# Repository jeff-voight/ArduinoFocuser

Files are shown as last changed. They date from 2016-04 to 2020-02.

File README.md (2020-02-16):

# ArduinoFocuser
My homemade Arduino Focuser

### Parts List
|ID				|#	|Name					|Type								|Module										|Description|
| ---			| ---	| ---					| ---								| ---										| ---										|
|A1				|1	|Arduino_UNO_R3			|MCU_Module:Arduino_UNO_R3			|Module:Arduino_UNO_R3						|Arduino UNO Microcontroller Module, release 3|
|C1, C2, C3		|3	|.01uF					|Device:C							|Capacitor_THT:C_Disc_D3.0mm_W2.0mm_P2.50mm	|Unpolarized capacitor|
|DRV1			|1	|Pololu_Breakout_DRV8825|Driver_Motor:Pololu_Breakout_DRV8825|Module:Pololu_Breakout-16_15.2x20.3mm		|Pololu Breakout Board, Stepper Driver DRV8825|
|Motor1			|1	|Stepper_Motor_bipolar	|Motor:Stepper_Motor_bipolar		|TerminalBlock:TerminalBlock_bornier-4_P5.08mm|4-wire bipolar stepper motor|
|R1, R2, R3, R4	|4	|10k					|Device:R							|Resistor_THT:R_Axial_DIN0204_L3.6mm_D1.6mm_P5.08mm_Horizontal|Resistor|
|SW1			|1	|Rotary_Encoder_Switch	|Device:Rotary_Encoder_Switch		|Rotary_Encoder:RotaryEncoder_Alps_EC11E-Switch_Vertical_H20mm|Rotary encoder, dual channel, incremental quadrate outputs, with switch|
|U1				|1	|DHT11					|Sensor:DHT11						|Sensor:Aosong_DHT11_5.5x12.0_P2.54mm		|Temperature and humidity module|
|U2				|1	|SN74HC14N				|dk_Logic-Gates-and-Inverters:SN74HC14N|digikey-footprints:DIP-14_W3mm			|IC INVERTER SCHMITT 6CH 14DIP|

* One (1) case of your choosing (plans for printing a sloppy case are included in the project)
* One (1) Motor mount (PDF somehwere around here for a 18ga steel bracket you can drill and bend yourself)
* One (1) coupler (I went with a 4mm x 6mm flexible coupler and drilled it to fit my shafts)
* One (1) 12VDC 2A power supply (wall-wart. You're just plugging it in to the Arduino UNOr3)
* Solder, wires, 4 pin connectors for as many scopes as you have.
* One long USB-A to USB-2 cable (or whatever the distance is from your laptop USB hub to where the focuser box will sit plus tripping slack)

# Things you'll want to change in the code:
My telescope focuser knob turns 5.75 times to go from end to end and moves some 13cm (or was it 23?). EncoderPositioner.h and StepperMotor.h are important.

For now, there may very-well be hardcoded values in the cpp files. I highly recommend you walk through them before applying bizarre amounts of
torque to your telescope focuser rod.

# To do:
* I want to add a limit switch to the motor end of the focus tube to detect the zero point. I haven't figured out how I want to impliment this. Maybe have the
focuser rack all the way closed on startup and then return to where it was. The problem I have with this is the people who have more than one telescope and 
maybe get the wiring wrong, causing their scope to rack focus out until it runs out of travel space and stalls the motor while seeking for the limit switch.

* Build a better case. For whatever reason, I can't get mine to close all the way and I'm pretty certain that I'm generating enough heat inside the box to affect
the DHT11 mounted on the side.

* Add links to a digikey BOM to order overthing.

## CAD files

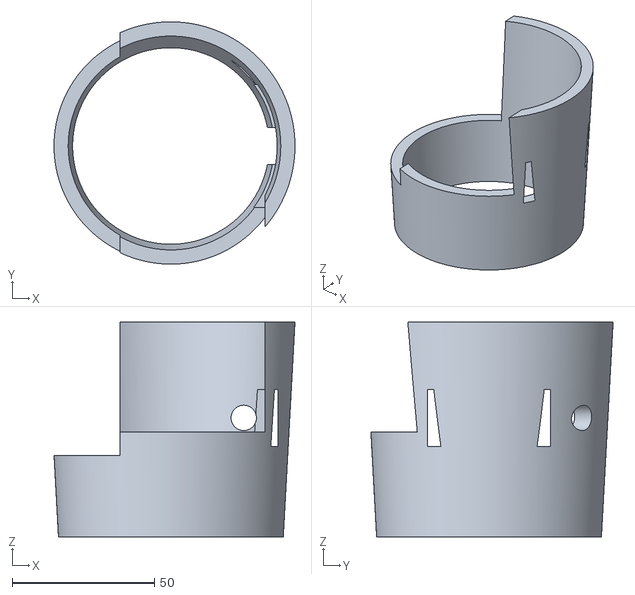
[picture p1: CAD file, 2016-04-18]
ArduinoFocuser/MotorMount.stl
84.7 x 85.1 x 75.3

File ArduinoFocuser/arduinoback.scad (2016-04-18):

caseLength=110-4;
caseWidth=100;
caseHeight=60-3;
caseThickness=2;
$fn=30;


    caseBack(caseLength, caseWidth, caseThickness);
    rotate([0, -90, 0]){
        caseFront(caseWidth, caseHeight, caseThickness);
    }
    translate([72, 83, caseThickness]){
        rotate([0,0, -90])
            smallProtoStandoff();
    }



module caseFront(width, height, thickness){
    difference(){
    cube([height, width, thickness]);
        //translate([4,4,0]) screwHole(1.5, thickness);
        translate([height-3.5, 3.5, 0]) backscrewHole(1.5, thickness);
        translate([height-3.5, width-3.5, 0]) backscrewHole(1.5, thickness);
        //translate([4, width-4, 0]) screwHole(1.5, thickness);
        translate([thickness+6, 28, 0]) cube([13, 12, thickness]);
        translate([thickness+6, 59, 0]) cube([14, 13, thickness]);
        translate([thickness+25, 36, 0]) cube([8, 21.25, thickness]);
    }
}

module caseBack(length, width, thickness){
    difference(){
    cube([length, width, thickness]);
        translate([3.5,3.5,0]) screwHole(1.5, thickness);
        translate([length-3.5, 3.5, 0]) screwHole(1.5, thickness);
        translate([length-3.5, width-3.5, 0]) screwHole(1.5, thickness);
        translate([3.5, width-3.5, 0]) screwHole(1.5, thickness);
    }
    
    translate([0,width/2-53/2,thickness]){
        translate([15.5, 6.5, 0])
            standoff(4, 1.5);
        translate([17, 53.8, 0])
            standoff(4, 1.5);
        translate([67.3, 10.5, 0])
            standoff(4, 1.5);
        translate([67.3, 38.5, 0])
            standoff(4, 1.5);
    }
}

module screwHole(radius, thickness){
    cylinder(thickness, radius+.5, radius);
}

module backscrewHole(radius, thickness){
    cylinder(thickness, radius, radius+1);
}

module standoff(standoffHeight, screwRadius){
	overage=2;
	difference(){
		cylinder(standoffHeight, r=screwRadius+overage);        
		cylinder(standoffHeight, r=screwRadius);
	}
}


module smallProtoStandoff(){
    translate([2.25, 2.25, 0]) standoff(3, 1.5);
    translate([67.75, 2.25, 0]) standoff(3,1.5);
    translate([2.25, 27.75, 0]) standoff(3,1.5);
    translate([67.75, 27.75, 0]) standoff(3,1.5);
}

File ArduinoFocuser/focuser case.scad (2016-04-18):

caseLength=110;
caseWidth=100;
caseHeight=60;
caseThickness=2;
standoffHeight=4;
caseScrewHeight=7;
$fn=30;


topPanel(caseLength, caseWidth, caseThickness);
translate([0, 0,  0]){
    rotate([90, 0, 0]){
        leftPanel(caseLength, caseHeight, caseThickness);
    }
}
translate([0 , caseWidth+caseThickness, 0]){
    rotate([90, 0, 0]){
        rightPanel(caseLength, caseHeight, caseThickness);
    }
}

translate([0,-1*caseThickness,0]){
    rotate([0, -90, 0]){
        endPanel(caseHeight, caseWidth+caseThickness*2, caseThickness);
    }
}

module topPanel(length, width, thickness){
    xor(){
        cube([length, width, thickness]);
        translate([5, 5, 0])
            knobBore(thickness);
        translate([29, 5, 0])
            buttonBoard(caseThickness);
        translate([6, 50, 0]){
            LCD_Panel(caseThickness);
        }
    }
    
//    translate([length-caseThickness-caseScrewHeight, width-caseScrewHeight, caseScrewHeight-caseThickness]){        
//            screwSocket(caseScrewHeight, caseThickness, 1);        
//    }
    translate([length-caseScrewHeight-caseThickness, 0, caseScrewHeight-caseThickness*2]){        
            screwSocket(caseScrewHeight, caseThickness, 1);        
    }
}

module leftPanel(length, width, thickness){
    cube([length, width, thickness]);
    translate([caseThickness, width-caseThickness, 2-caseThickness]){
        verticalScrewSocket(caseScrewHeight, caseThickness, 1);
    }
    translate([length-caseThickness-caseScrewHeight, width-caseThickness, caseThickness-2]){
        verticalScrewSocket(caseScrewHeight, caseThickness, 1);
    }
}

module rightPanel(length, width, thickness){
    cube([length, width, thickness]);
    translate([caseThickness, width-caseThickness, caseThickness+caseScrewHeight]){
        verticalScrewSocket(caseScrewHeight, caseThickness, 1);
    }
    translate([length-caseThickness-caseScrewHeight, width-caseThickness, caseScrewHeight+2]){
        verticalScrewSocket(caseScrewHeight, caseThickness, 1);
    }
}

module endPanel(length, width, thickness){
    mirror([0, 0, 180])
    xor(){
        cube([length, width, thickness]);
        translate([20, 40, 0])
            tempBore(caseThickness);
        
    }
}

module LCD_Panel(caseThickness){
    lcdPanelLength=98;
    lcdPanelWidth=40;
    screwOffsetX=2.075;
    screwOffsetY=-7.675;
    cube([lcdPanelLength, lcdPanelWidth, caseThickness]);
    translate([screwOffsetX, screwOffsetY, caseThickness]) standoff(5, 1.2);  // TO DO: Correct location
    translate([lcdPanelLength-screwOffsetX, lcdPanelWidth-screwOffsetY, caseThickness]) standoff(5, 1.2);
    translate([screwOffsetX, lcdPanelWidth-screwOffsetY, caseThickness]) standoff(5, 1.2);
    translate([lcdPanelLength-screwOffsetX, screwOffsetY, 1]) standoff(5, 1.2);
}

module knobBore(caseThickness){
    mountThickness=1;
    standoffKnobSquareBore=14.5;
    standoffKnobSquareHeight=6;
    // outer walls
    standoffBoxSize=standoffKnobSquareBore+mountThickness*2;
    standoffKnobBore=9;
    standoffKnobBoreDepth=5.8;
    standoffKnobHole=3.5;
    standoffBoxHeight=standoffKnobBoreDepth+standoffKnobSquareHeight;
    translate([1, 2, 0]){
    difference(){
//    // Rectangular Holder
            translate([0,0,caseThickness])
                cube([standoffBoxSize,   standoffBoxSize, standoffBoxHeight]);        
            translate([(standoffBoxSize-standoffKnobBore)/2, (standoffBoxSize-standoffKnobBore)/2, caseThickness]) 
                cube(standoffKnobBore, standoffKnobBore, standoffKnobBoreDepth);
            translate([mountThickness, mountThickness, caseThickness+standoffKnobBoreDepth])
                cube([standoffKnobSquareBore, standoffKnobSquareBore, standoffKnobSquareHeight]);
            
        };
        translate([standoffBoxSize/2, standoffBoxSize/2, 0])
            cylinder(caseThickness, r=standoffKnobHole);
    }
    translate([16, 25, caseThickness]) standoff(standoffBoxHeight, 1.5);
}

module buttonBoard(){

    translate([11.2, 7.35, 0]) Button_Holder(caseThickness);
    translate([12.2, 18.35, 0]) LED_Holder(caseThickness);

    translate([26.4, 7.35, 0]) Button_Holder(caseThickness);
    translate([27.2, 18.35, 0]) LED_Holder(caseThickness);

    translate([41.6, 7.35, 0]) Button_Holder(caseThickness);
    translate([42.2, 18.35, 0]) LED_Holder(caseThickness);

    translate([56.8, 7.35, 0]) Button_Holder(caseThickness);
    translate([57.2, 18.35, 0]) LED_Holder(caseThickness);
    
    translate([2.25, 2.25, caseThickness]) standoff(3, 1.5);
    translate([67.75, 2.25, caseThickness]) standoff(3,1.5);
    translate([2.25, 27.75, caseThickness]) standoff(3,1.5);
    translate([67.75, 27.75, caseThickness]) standoff(3,1.5);
    
}


/*module standoff(standoffHeight, screwRadius){
	overage=1;
	difference(){
		cylinder(standoffHeight, r=screwRadius+overage);
		cylinder(standoffHeight, r=screwRadius);
	}
}*/


module Button_Holder(caseThickness){
    buttonHoleRadius=4;
    cylinder(caseThickness, buttonHoleRadius*1.7, buttonHoleRadius);
    cylinder(caseThickness-1, r=buttonHoleRadius*1.7);

}

module LED_Holder(caseThickness){

    ledRadius=3;
    cylinder(caseThickness, r=ledRadius);
}



module tempBore(caseThickness){
    mountThickness=1;
    standoffSquareBoreWidth=15;
    standoffSquareBoreLength=19;
    standoffSquareHeight=2;
    standoffBoxSize=standoffSquareBoreWidth+mountThickness*2;    
    translate([1.5, 1.5, 0]){
        difference(){
            translate([0,0,caseThickness])
                cube([standoffSquareBoreWidth+mountThickness*2,standoffSquareBoreLength+mountThickness*2, standoffSquareHeight]);        
            translate([mountThickness, mountThickness, 0]) 
                cube([standoffSquareBoreWidth, standoffSquareBoreLength, standoffSquareHeight+caseThickness+1]);
     
        };
        translate([mountThickness, mountThickness, 0]) 
            cube([standoffSquareBoreWidth, standoffSquareBoreLength,caseThickness]);
        
    }
    translate([1.5+(mountThickness+standoffSquareBoreWidth)/2, 25, caseThickness]) standoff(standoffSquareHeight, 1.5);
}


module standoff(standoffHeight, screwRadius){
	overage=2;
	difference(){
		cylinder(standoffHeight, r=screwRadius+overage);
        
            cylinder(standoffHeight, r=screwRadius);
	}
}

module screwSocket(standoffHeight, caseDepth, screwRadius){
    overage=1;
    boxSize=standoffHeight;//+overage*2;
    difference(){
		cube(boxSize);
        rotate([90, 0, 90]){
        translate([boxSize/2, boxSize/2, 0]){            
                cylinder(boxSize, r=screwRadius);
            }
        }
    }
}

module verticalScrewSocket(standoffHeight, caseDepth, screwRadius){
    overage=1;
    boxSize=standoffHeight;//+overage*2;
   rotate([0, -270, -90])
    difference(){
		cube(boxSize);        
        translate([boxSize/2, boxSize/2, 0]){            
                cylinder(boxSize, r=screwRadius);
            }
       }
}

module xor(){
    difference(){
        union(){
            children(0);
//            children(1);
            children([1:$children-1]);
        };
        intersection(){
            children(0);
//            children(1);
            children([1:$children-1]);
        }
    }
}

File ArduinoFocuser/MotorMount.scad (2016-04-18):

$fn=360;
boreBaseRadius=69/2;
boreTopRadius=77.2/2;
boreLength=75.35;
focusRod=8.9/2;
focusRodProtusion=30; // TO DO: Measure this
focusRodHolderWidth=43.2;
focusRodHolderLength=20; // TO DO: Measure this
focusRodCenterOffset=41.75;
focusRodRackWidth=12.0;
maxClamshellLength=28.6;
focusRodOffset=28.25;
focusRodInset=1;
focusRodLength=110;
finderBaseWidth=20;
finderBaseLength=30;

difference(){
    outerShell();
    telescopeBore();
}

module telescopeBore(){
    cylinder(boreLength, boreBaseRadius, boreTopRadius);
    translate([boreTopRadius-13, 0, focusRodCenterOffset]){
        cube([24, focusRodHolderWidth, focusRodHolderLength], center=true);
        rotate([90, 0, 0]){
            cylinder(focusRodLength, r=focusRod, center=true);
        }
    }
    translate([boreBaseRadius/2, 0, focusRodCenterOffset/2]){
        cube([focusRodCenterOffset, 13, focusRodCenterOffset], center=true);
    }
    translate([-1.5*boreTopRadius, -1*boreTopRadius, maxClamshellLength]){
        cube([finderBaseWidth*2, finderBaseLength*3, boreLength-maxClamshellLength]);
    }
    translate([-.7*boreTopRadius, -2*boreTopRadius, focusRodCenterOffset-5]){
        cube([finderBaseWidth*3, finderBaseLength*3, boreLength-focusRodCenterOffset+5]);
    }
}

module outerShell(){
    cylinder(boreLength, boreBaseRadius+5, boreTopRadius+5);
}

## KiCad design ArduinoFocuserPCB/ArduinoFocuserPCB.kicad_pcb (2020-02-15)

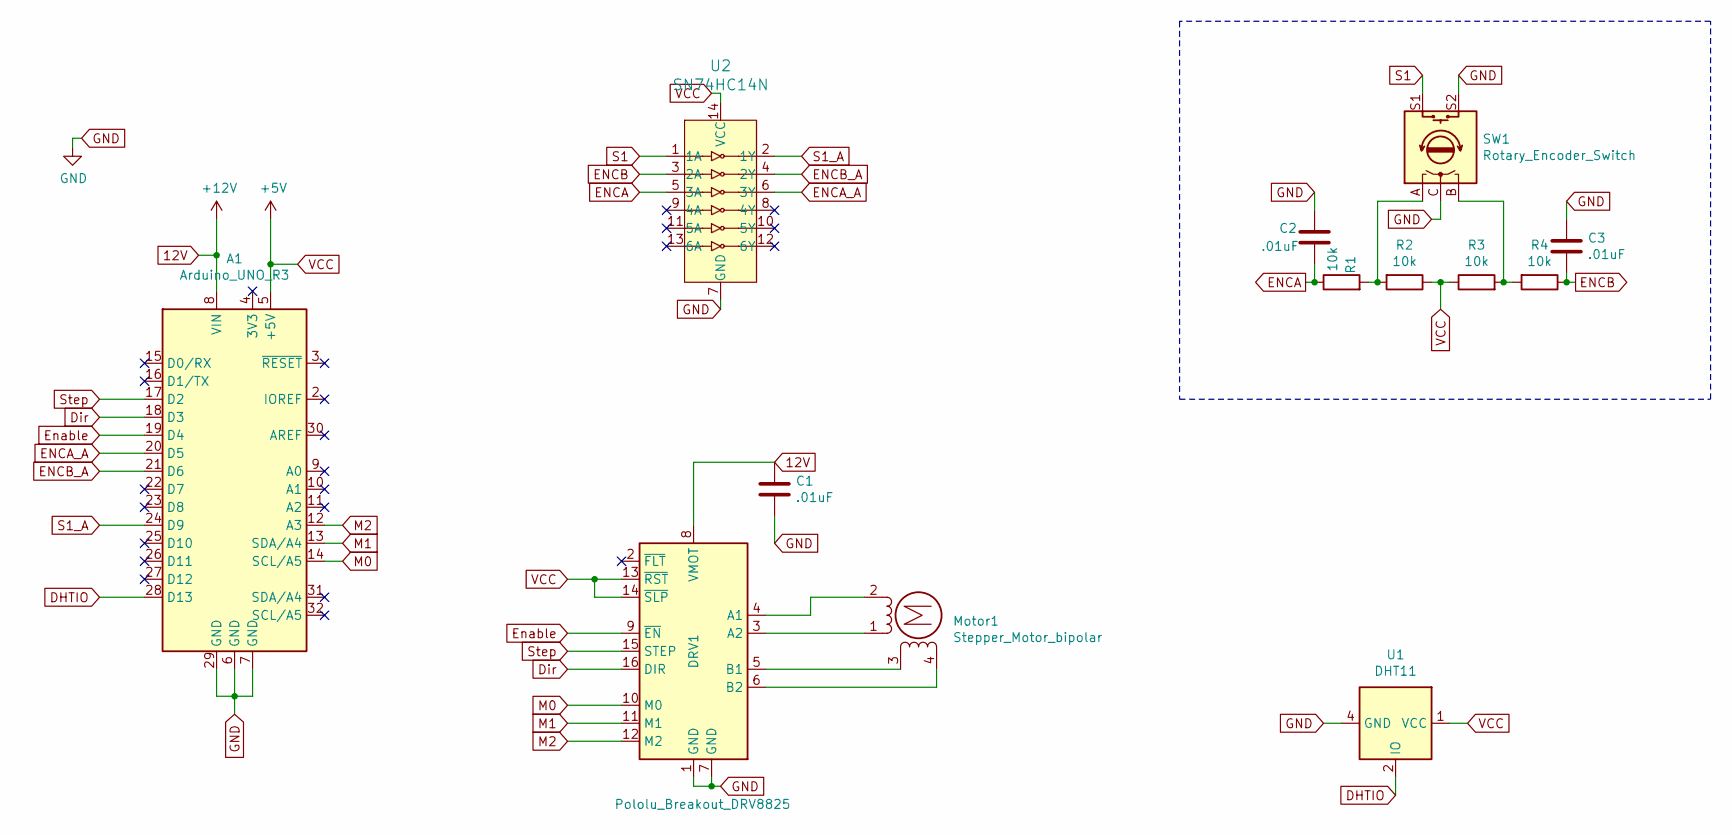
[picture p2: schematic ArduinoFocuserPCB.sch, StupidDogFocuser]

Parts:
A1: Arduino_UNO_R3
C1, C2, C3: .01uF; C_Disc_D3.0mm_W2.0mm_P2.50mm
DRV1: Pololu_Breakout_DRV8825; Pololu_Breakout-16_15.2x20.3mm
Motor1: Stepper_Motor_bipolar; TerminalBlock_bornier-4_P5.08mm
R1, R2, R3, R4: 10k; R_Axial_DIN0204_L3.6mm_D1.6mm_P5.08mm_Horizontal
SW1: Rotary_Encoder_Switch; RotaryEncoder_Alps_EC11E-Switch_Vertical_H20mm
U1: DHT11; Aosong_DHT11_5.5x12.0_P2.54mm
U2: SN74HC14N; DIP-14_W3mm; MPN SN74HC14N; Digi-Key_PN 296-1577-5-ND

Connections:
12V: A1.8 (VIN), C1.1, DRV1.8 (VMOT)
DHTIO: A1.28 (D13), U1.2 (IO)
Dir: A1.18 (D3), DRV1.16 (DIR)
ENCA: C2.2, R1.1, U2.5 (3A)
ENCA_A: A1.20 (D5), U2.6 (3Y)
ENCB: C3.2, R4.1, U2.3 (2A)
ENCB_A: A1.21 (D6), U2.4 (2Y)
Enable: A1.19 (D4), DRV1.9 (~EN)
GND: A1.6 (GND), A1.7 (GND), A1.29 (GND), C1.2, C2.1, C3.1, DRV1.1 (GND), DRV1.7 (GND), SW1.C, SW1.S2, U1.4 (GND), U2.7 (GND)
M0: A1.14 (SCL/A5), DRV1.10 (M0)
M1: A1.13 (SDA/A4), DRV1.11 (M1)
M2: A1.12 (A3), DRV1.12 (M2)
unnamed: DRV1.3 (A2), Motor1.1
unnamed: DRV1.4 (A1), Motor1.2 (-)
unnamed: DRV1.5 (B1), Motor1.3
unnamed: DRV1.6 (B2), Motor1.4
unnamed: R1.2, R2.2, SW1.A
unnamed: R3.2, R4.2, SW1.B
S1: SW1.S1, U2.1 (1A)
S1_A: A1.24 (D9), U2.2 (1Y)
Step: A1.17 (D2), DRV1.15 (STEP)
VCC: A1.5 (+5V), DRV1.13 (~RST), DRV1.14 (~SLP), R2.1, R3.1, U1.1 (VCC), U2.14 (VCC)

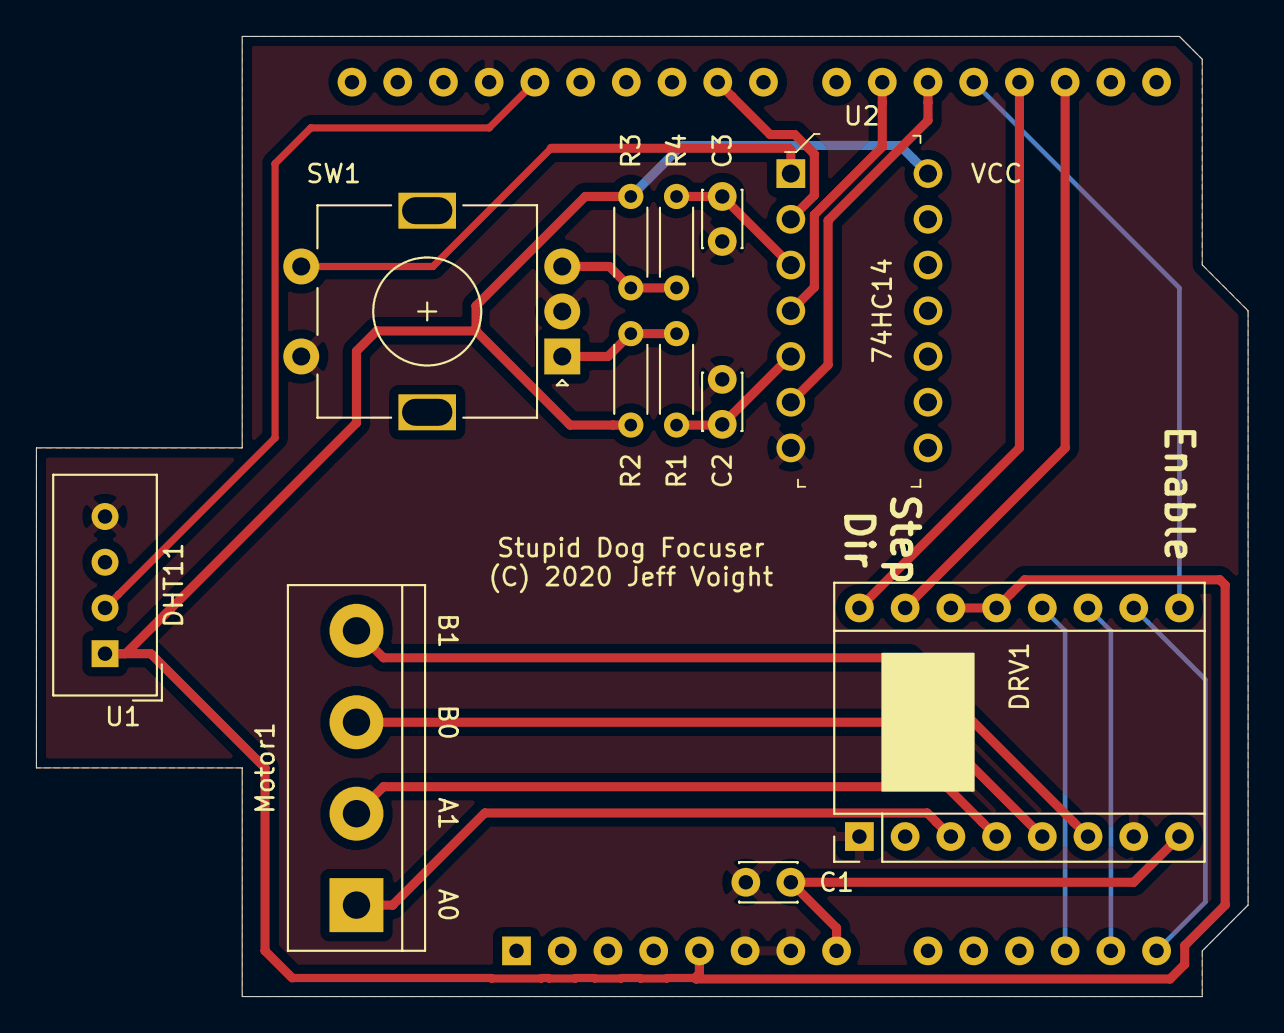
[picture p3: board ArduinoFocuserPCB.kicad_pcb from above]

Board: 2 copper layers, 67.3 x 53.3 mm, 13 parts (1 on the bottom side), 22 nets.

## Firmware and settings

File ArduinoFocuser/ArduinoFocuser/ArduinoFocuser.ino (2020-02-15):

#include <LiquidCrystal.h>

/*
  Name:		ArduinoFocuser.ino
  Created:	4/12/2016 11:12:14 AM
  Author:	jeff
*/

// the setup function runs once when you press reset or power the board
#include "StepperMotor.h"
#include "LCDDisplay.h"
#include "TemperatureSensor.h"
#include "ArduinoCircuit.h"
#include "PushButton.h"
#include "EncoderPositioner.h"
#include "Positioner.h"

PushButton reset, lowLimit, highLimit, turbo;
uint8_t resetButtonPin = 4, resetLEDPin = A0, lowLimitButtonPin = 5, lowLimitLEDPin = A1,
        highLimitButtonPin = 6, highLimitLEDPin = A2, turboButtonPin = 7, turboLEDPin = A3;


EncoderPositioner encoderPositioner;
uint8_t encoderPositionerPinA = 2, encoderPositionerPinB = 3;


TemperatureSensor temperatureSensor;
uint8_t temperatureSensorPinA = 8;


LCDDisplay lcd;

StepperMotor stepperMotor;
uint8_t rstPin = 13, stepPin = 10, dirPin = 11, stepSizePin = 12;

// ASCOM/INDI commands
String halt = "HALT", move = "MOVE", isMoving = "MOVING", absolute = "ABSOLUTE",
       position = "POSITION", temperature = "TEMPERATURE", disconnect = "DISCONNECT";
char commandDelimiter = '#';

/* Run before loop.
    Initialize serial communications, all buttons, the encoder and interrupts, the temperature sensor
    lcd, and monitor.
*/
void setup() {
  Serial.begin(115200);
  Serial.println("StupidDog.v1.1");
  reset = PushButton(resetButtonPin, resetLEDPin);
  turbo = PushButton(turboButtonPin, turboLEDPin);

  encoderPositioner = EncoderPositioner(encoderPositionerPinA, encoderPositionerPinB, reset, turbo);
  attachInterrupt(0, interruptA, CHANGE);
  attachInterrupt(1, interruptB, CHANGE);

  temperatureSensor = TemperatureSensor(temperatureSensorPinA);

  lcd = LCDDisplay(&encoderPositioner, temperatureSensor);

  stepperMotor = StepperMotor(rstPin, stepPin, dirPin, stepSizePin, &encoderPositioner);
}

// the loop function runs over and over again until power down or reset
void loop() {
  int8_t suppressTempCounter=0;
  int8_t suppressLCDCounter=0;
  String cmdString, cmd, param;

  if (Serial.available() > 0) {
    cmdString = Serial.readStringUntil(commandDelimiter);

    // Check for separator character
    uint8_t separatorPosition = cmdString.indexOf(":");

    // Parse command if there's a separator
    if (separatorPosition != -1) {
      cmd = cmdString.substring(0, separatorPosition);
      param = cmdString.substring(separatorPosition + 1);
    } else {
      cmd = cmdString;
    }

    if(cmd == move) {
        encoderPositioner.moveRelative(param.toInt());
        Serial.print(encoderPositioner.getPosition()); Serial.println("#");
    } 
    else if(cmd == position){
        Serial.print(encoderPositioner.getPosition()); Serial.println("#");
    }
    else if(cmd == isMoving){
        Serial.println((stepperMotor.isMoving() ? "TRUE#" : "FALSE#"));
    }
    else if(cmd == temperature){
        int temp = temperatureSensor.getTemperature();
        Serial.print(temp); Serial.println("#");
    }
    else if(cmd == halt){
        encoderPositioner.halt();
        Serial.print(encoderPositioner.getPosition()); Serial.println("#");
    }
    else if(cmd == disconnect){
        stepperMotor.disconnect();
        Serial.println("DISCONNECTED#");
    }
  }

  encoderPositioner.refresh();

  if(suppressLCDCounter--<=0){
    lcd.refresh();
    suppressLCDCounter=255;
  }

  stepperMotor.refresh();
}

// Interrupt routines to trigger the encoder
void interruptA() {
  encoderPositioner.interruptA();
}

void interruptB() {
  encoderPositioner.interruptB();
}

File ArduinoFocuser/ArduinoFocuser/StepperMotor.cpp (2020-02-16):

// 
// 
// 

#include "StepperMotor.h"

StepperMotor::StepperMotor()
{
}

StepperMotor::StepperMotor(short _rstPin, short _stepPin, short _dirPin, short _stepSizePin, Positioner * _positioner)
{
	rstPin = _rstPin;
	stepPin = _stepPin;
	dirPin = _dirPin;
	stepSizePin = _stepSizePin;
	positioner = _positioner;
  stepper = AccelStepper(1, _stepPin, _dirPin);
  stepper.setMaxSpeed(800);
  stepper.setAcceleration(200);
  
	pinMode(rstPin, OUTPUT);
	digitalWrite(rstPin, HIGH);
	pinMode(stepSizePin, OUTPUT);
  pinMode(stepSizePin, LOW);
}

StepperMotor::~StepperMotor()
{
}

void StepperMotor::refresh()
{
	change = positioner->getChange();
  long currentPosition = stepper.currentPosition()+change;
	if (change != 0) {
		stepper.runToNewPosition(currentPosition);
	}
  positioner->setChange(0);
  positioner->setPosition(currentPosition);
}

bool StepperMotor::isMoving()
{
	return stepper.isRunning();
}

bool StepperMotor::disconnect()
{
	digitalWrite(rstPin, LOW);
	return true;
}

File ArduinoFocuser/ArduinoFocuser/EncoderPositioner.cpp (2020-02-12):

// 
// 
// 

#include "EncoderPositioner.h"

EncoderPositioner::EncoderPositioner()
{
	pinA = 0;
	pinB = 0;
	
}

EncoderPositioner::EncoderPositioner(char _pinA, char _pinB, PushButton _resetButton, PushButton _turboButton)
{
	pinA = _pinA;
	pinB = _pinB;
	resetButton = _resetButton;
	turboButton = _turboButton;
	pinMode(pinA, INPUT);
	pinMode(pinB, INPUT);
  oldA = digitalRead(pinA);
  oldB = digitalRead(pinB);
}


EncoderPositioner::~EncoderPositioner()
{
}

void EncoderPositioner::increment(long _change)
{
	if (turboButton.isPushed()) {
		addChange(_change*turboMultiplier);
	} else {
		addChange(_change);
	}
}


void EncoderPositioner::refresh() {
  
	if (highLimit-limitThreshold < position) {
		highLimitButton.setLED(true);
	} else {
		highLimitButton.setLED(false);
	}
 
	if (lowLimit+limitThreshold > position) {
		lowLimitButton.setLED(true);
	} else {
		lowLimitButton.setLED(false);
	}
 
	resetButton.refresh();
	lowLimitButton.refresh();
	highLimitButton.refresh();
	turboButton.refresh();
  
	if (resetButton.isPushed()) {
		halt();
	}
 
	if (resetButton.isHeld()) {
		if (lowLimitButton.isPushed()) {
			//Serial.println("Resetting low limit.");
			setLowLimit(getPosition());
		}
		if (highLimitButton.isPushed()) {
			//Serial.println("Resetting high limit.");
			setHighLimit(getPosition());
		}
		if (lowLimitButton.isHeld()) {
			//Serial.println("Clearing low limit.");
			setLowLimit(-2147483647);
		}
		if (highLimitButton.isHeld()) {
			//Serial.println("Clearing high limit.");
			setHighLimit(2147483647);
		}
	}
}

void EncoderPositioner::interruptA()
{
	if ((long)(micros() - lastMicros) < debouncingTime * 1000) {
		return;
	}
	lastMicros = micros();
	int A = digitalRead(pinA);
	oldB = digitalRead(pinB);
	
	if (A == oldA) {
		return;
	}
	oldA = A;
	if (A == HIGH) {
		if (oldB == HIGH) {
			increment(-1); // CW
		} else {
			increment(1); // CCW
		}
	} else {
		if (oldB == LOW) {
			increment(-1);// CW
		} else {
			increment(1);// CCW
		}
	}
}

void EncoderPositioner::interruptB()
{
	if ((long)(micros() - lastMicros) < debouncingTime * 1000) {
		return;
	}
	lastMicros = micros();
	int B = digitalRead(pinB);
	oldA = digitalRead(pinA);
	
	if (B == oldB) {
		return;
	}
	oldB = B;
	if (B == HIGH) {
		if (oldA == HIGH) {
			increment(1);// CW
		} else {
			increment(-1);// CCW
		}
	} else {
		if (oldA == LOW) {
			increment(1);// CW
		} else {
			increment(-1);// CCW
		}
	}
}

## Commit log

2016-04-14 Only missing limit setters and ASCOM drivers. Probably filled with bugs.
    [ArduinoFocuser.ino, EncoderPositioner.cpp, Positioner.h]
2016-04-16 Still have a cycling positioner bug
    [ArduinoFocuser.ino, EncoderPositioner.cpp, Positioner.h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]
2016-04-17 Changed something. Lord knows what. Probably stepper stuff.
2016-04-18 ASCOM Driver and commands
2016-04-18 Added circuit diagram
2016-04-18 Added motor mount 3d printer models
    [MotorMount.scad, MotorMount.stl]
2016-04-18 Added case diagrams for 3d printer
    [arduinoback.scad, focuser case.scad]
2016-04-18 some file is missing
    [ArduinoFocuser.ino, EncoderPositioner.cpp]
2016-04-18 Added a suspend so upon close, I can disconnect the motor.
2020-01-27 Revert "Added unsigned to the micros() and last micros()"
    This reverts commit c66d8b4b85dd3000e5163930f08a163de1e70bb6.
    [ArduinoFocuser.ino, EncoderPositioner.cpp, Positioner.h]
2020-02-11 created pcb files
    [ArduinoFocuserPCB.kicad_pcb, ArduinoFocuserPCB.sch]
2020-02-11 wired up
2020-02-11 created traces
    [ArduinoFocuserPCB.sch]
2020-02-15 trigger added. some routing. needed restart checkpoint
    [ArduinoFocuserPCB.sch]
2020-02-15 git ignore
    [ArduinoFocuserPCB.kicad_pcb, ArduinoFocuserPCB.sch]
2022-02-11 Bump Google.Protobuf in /ArduinoFocuser/VoightFocuserDriver
    Bumps [Google.Protobuf](https://github.com/protocolbuffers/protobuf) from 3.7.0 to 3.15.0.
    - [Release notes](https://github.com/protocolbuffers/protobuf/releases)
    - [Changelog](https://github.com/protocolbuffers/protobuf/blob/master/generate_changelog.py)
    - [Commits](https://github.com/protocolbuffers/protobuf/compare/v3.7.0...v3.15.0)
    ---
    updated-dependencies:
    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
2026-01-21 Bump Newtonsoft.Json in /ArduinoFocuser/VoightFocuserDriver (#11)
    Bumps [Newtonsoft.Json](https://github.com/JamesNK/Newtonsoft.Json) from 10.0.3 to 13.0.1.
    - [Release notes](https://github.com/JamesNK/Newtonsoft.Json/releases)
    - [Commits](https://github.com/JamesNK/Newtonsoft.Json/compare/10.0.3...13.0.1)
    - dependency-name: Newtonsoft.Json
    dependency-type: direct:production
    ...
    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

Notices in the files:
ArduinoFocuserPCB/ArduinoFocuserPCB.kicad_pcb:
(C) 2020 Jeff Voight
